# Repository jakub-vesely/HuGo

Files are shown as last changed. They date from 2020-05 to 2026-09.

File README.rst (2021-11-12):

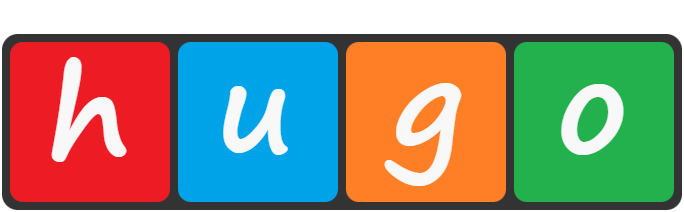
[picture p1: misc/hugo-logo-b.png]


Main goal of this project is to build a robotic car for my children. Although, it is designed as a common modular system with ambition to be used as a generic educative tool/toy.

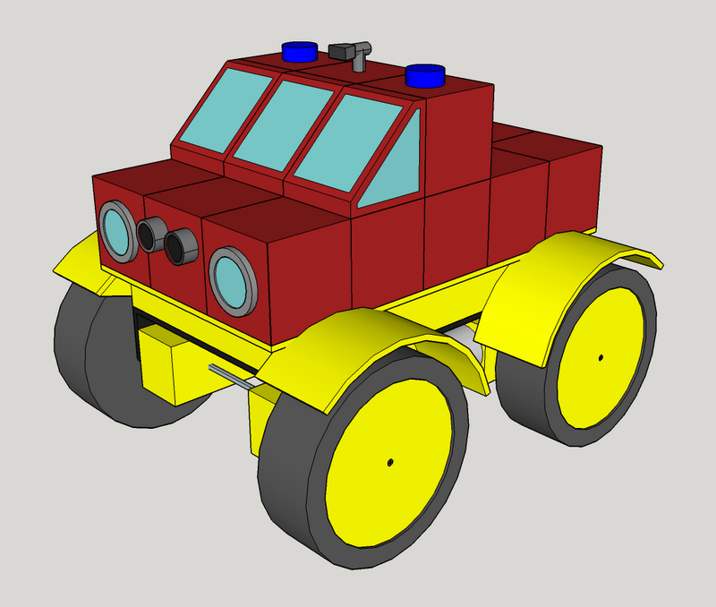
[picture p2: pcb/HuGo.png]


Current version of the Hugo project is based on ESP32, and Micropython. Extensive blocks (tyny-blocks) are based on AtTiny 412/416 micro-controllers running Arduino code.

project uses forked Micropython https://github.com/jakub-vesely/micropython. HuGo board specific code is located in the micropython/ports/esp32/boards/HUGO/ directory
and can be flashed by command:
"``idf.py -D MICROPY_BOARD=HUGO -B build-HUGO flash monitor -p <COM PORT>``"

-----
Usage
-----

Hugo specific scripts are stored in *micropython/ports/esp32/boards/HUGO/modules*. These files are already prebuilt to the firmware.
User defined behavior should be inserted to *tools/upload/events.py*. Hugo project is optimized for "events driven programming" hance all user defined actions should be added
via planned by one of these methods:

* **plan** (function, \*args, \**kwargs) for performance without expected delay
* **postpone** (delay_s, function, \*args, \**kwargs) for performance an action after a defined delay
* **repeat** (delay_s, function, \*args, \**kwargs) for continuous performed action with a defined delay

**Note**: These planner methods expects action method name defined as parameter **without brackets** followed by its parameters.

Planned action can be removed by the **kill** (handle) method. Appropriate handle is returned by method creating the event.
Programmed behavior can be uploaded to Hugo main block by launching script "``python hugo_terminal.py -f -m``" from the *tools* sub-directory.

Uploading will be performed wireless via BLE.

-----------
Development
-----------

Scripts already placed to firmware can be replaced by uploading files placed in *tools/develop* directory.
These files can be changed and uploaded to the Hugo main block by launching "``python hugo_terminal.py -f -m``" from the *tools* sub-directory.

For integration changes to firmware the original files in *micropython/ports/esp32/boards/HUGO/modules* have to be replaced by updated once.
This action can be performed by launching "``python devel_to_firmware.py``".

To build firmware esp-idf version 4 must be installed.
The build and upload to Hugo main block can be performed by launching:

"``idf.py -D MICROPY_BOARD=HUGO -B build-HUGO erase_flash flash monitor -p <COM PORT>``"
from the *micropython/ports/esp32/* directory.

The parameter *erase_flash* is recommended to remove previously uploaded scripts.

-------
Sources
-------

* Micropython homepage: https://micropython.org/
* Overview of ESP32 features is available here: https://www.espressif.com/en/products/socs/esp32/overview
* esp-idf is linked externally as recommended. Getting started guide is available here: https://docs.espressif.com/projects/esp-idf/en/stable/get-started/
* Arduino official web page https://www.arduino.cc/
* Arduino support for AtTiny series 0 and 1 https://github.com/SpenceKonde/megaTinyCore

----------
Deprecated
----------

* originally was the HuGo project based of LUA but this interpreter is not supported any more
* esp-idf project with LUA support has been moved to *src_deprecated* directory
* LUA 3.5.4 is part of the repository. Original source code is available here: https://www.lua.org/download.html

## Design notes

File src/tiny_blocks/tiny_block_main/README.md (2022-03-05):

This directory must be uploaded among Arduino libraries (Documents\Arduino\libraries) to be hugo_tiny_block_base_arduino.h visible for rest of tiny_block projects.

you can do it:
* in Windows by: mklink /D link_path source_directory_path
* in Linux by: ln -s source_directory_path link_path

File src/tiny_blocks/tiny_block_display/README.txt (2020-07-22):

hugo font derived from https://github.com/epto/epto-fonts/blob/master/font-images/img/leggibile-8x16.png
ssd1306.c derived from https://github.com/yanbe/ssd1306-esp-idf-i2c

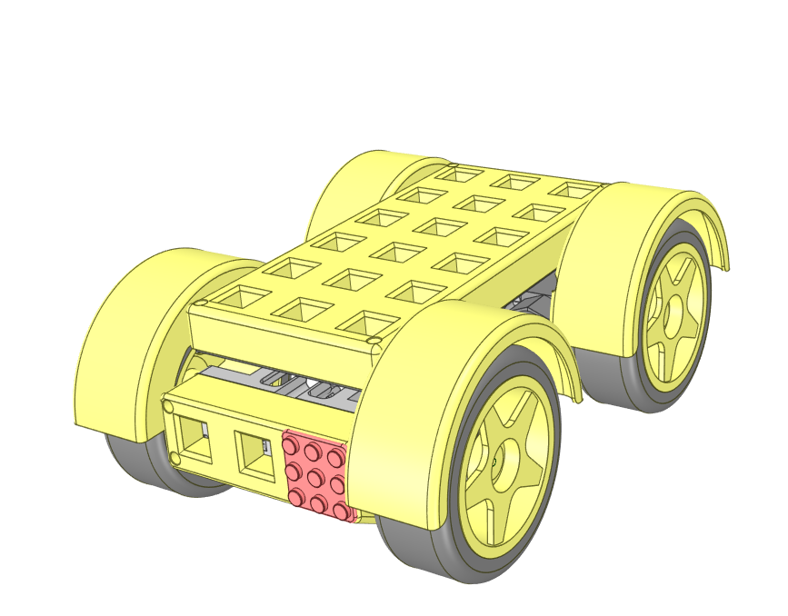
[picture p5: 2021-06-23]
shells/hugo_framework.png

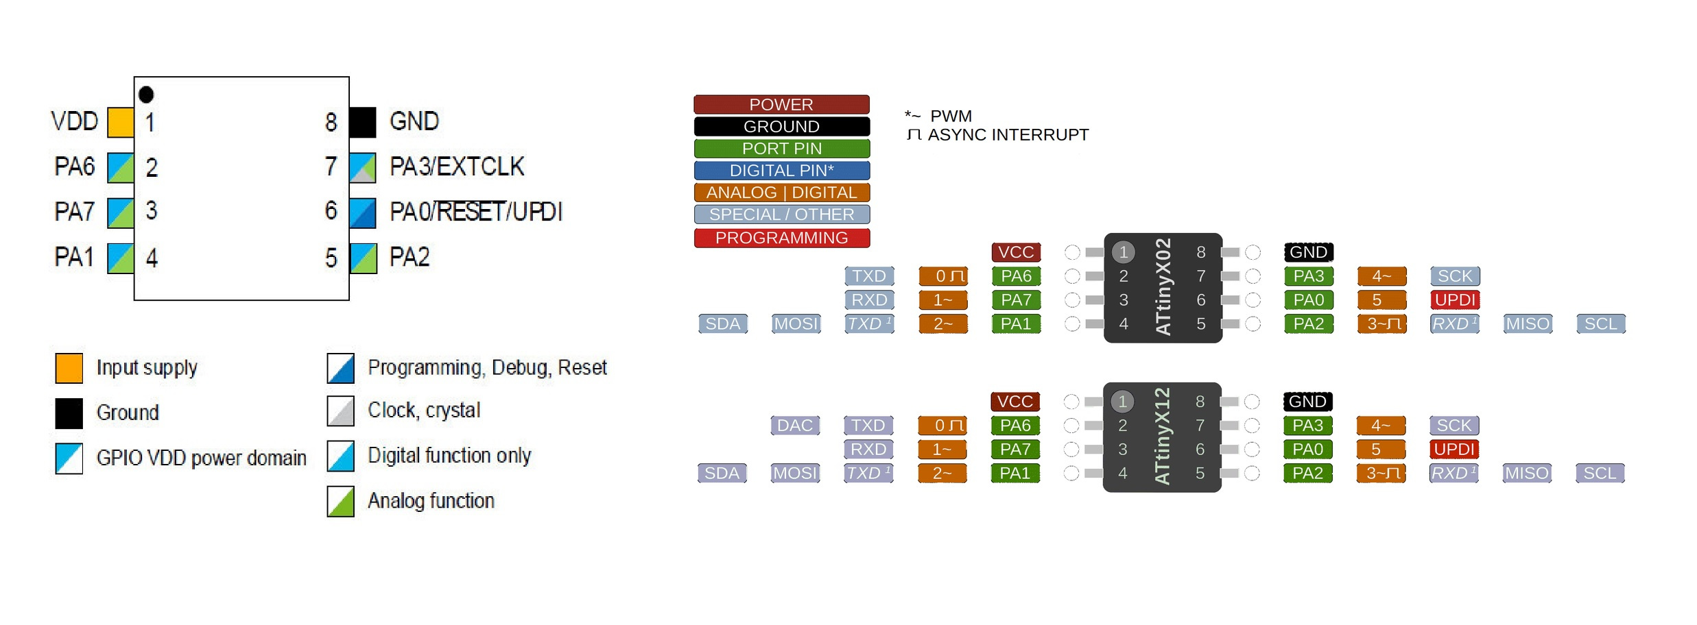
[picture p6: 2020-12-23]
pcb/datasheets/attinyX12.jpg

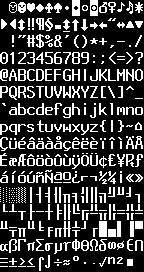
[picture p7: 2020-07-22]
src/tiny_blocks/tiny_block_display/font8x16.png

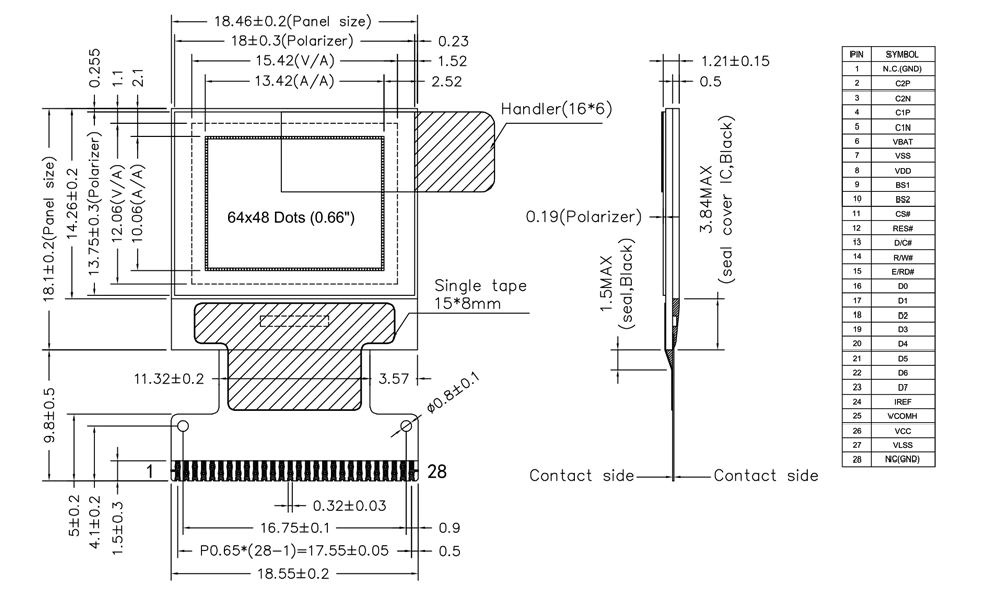
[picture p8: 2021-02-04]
pcb/datasheets/0-66-Inch-Graphic-64X48-White-LCD-28-Pin-Module-SSD1306-OLED-Micro-Display.jpg

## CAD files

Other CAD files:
pcb/hugo.skp

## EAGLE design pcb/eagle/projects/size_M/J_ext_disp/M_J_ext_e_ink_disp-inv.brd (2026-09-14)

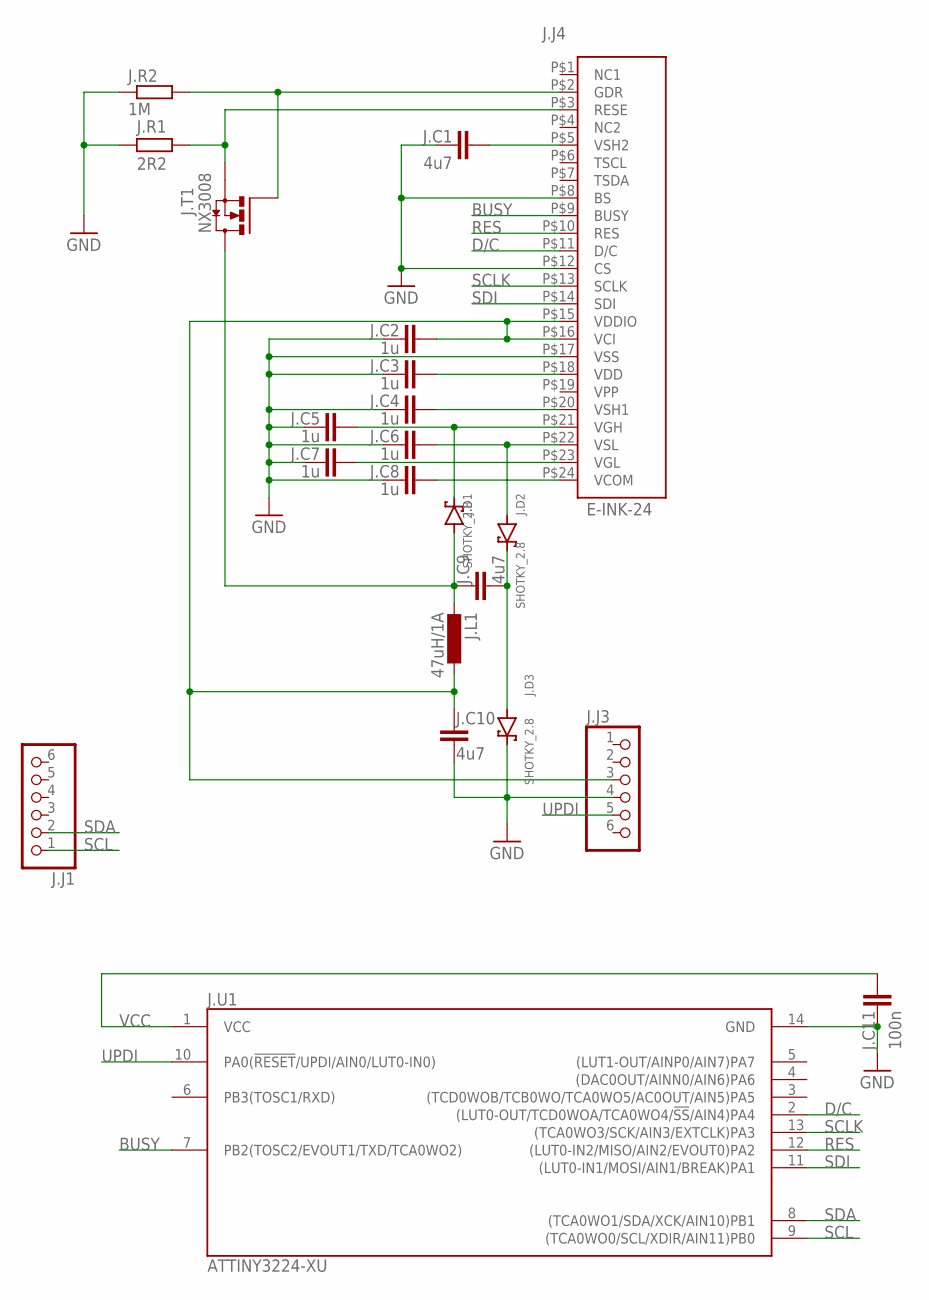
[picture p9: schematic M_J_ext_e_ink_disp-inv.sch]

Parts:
J.C1, J.C9, J.C10: 4u7; C0603
J.C2, J.C3, J.C4, J.C5, J.C6, J.C7, J.C8: 1u; C0603
J.C11: 100n; C0603
J.D1, J.D2, J.D3: SHOTKY_2.8
J.J1, J.J3: PINHD-1X6; 1X06
J.J4: E-INK-24
J.L1: 47uH/1A; L3230M
J.R1: 2R2; R0603
J.R2: 1M; R0603
J.T1: NX3008; SO23
J.U1: ATTINY3224-XU; TSSOP14

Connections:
BUSY: J.J4.P$9 (BUSY), J.U1.7 (PB2(TOSC2/EVOUT1/TXD/TCA0WO2))
D/C: J.J4.P$11 (D/C), J.U1.2 ((LUT0-OUT/TCD0WOA/TCA0WO4/!SS!/AIN4)PA4)
GND: J.C1.2, J.C2.2, J.C3.2, J.C4.2, J.C5.2, J.C6.2, J.C7.2, J.C8.2, J.C10.2, J.C11.2, J.D3.K (C), J.J3.4, J.J4.P$8 (BS), J.J4.P$12 (CS), J.J4.P$17 (VSS), J.R1.2, J.R2.1, J.U1.14 (GND)
unnamed: J.C1.1, J.J4.P$5 (VSH2)
unnamed: J.C8.1, J.J4.P$24 (VCOM)
unnamed: J.C6.1, J.D2.A, J.J4.P$22 (VSL)
unnamed: J.C5.1, J.D1.K (C), J.J4.P$21 (VGH)
unnamed: J.C9.2, J.D2.K (C), J.D3.A
unnamed: J.J4.P$3 (RESE), J.R1.1, J.T1.S
unnamed: J.C3.1, J.J4.P$18 (VDD)
unnamed: J.C4.1, J.J4.P$20 (VSH1)
unnamed: J.C9.1, J.D1.A, J.L1.2, J.T1.D
unnamed: J.C7.1, J.J4.P$23 (VGL)
unnamed: J.J4.P$2 (GDR), J.R2.2, J.T1.G
RES: J.J4.P$10 (RES), J.U1.12 ((LUT0-IN2/MISO/AIN2/EVOUT0)PA2)
SCL: J.J1.1, J.U1.9 ((TCA0WO0/SCL/XDIR/AIN11)PB0)
SCLK: J.J4.P$13 (SCLK), J.U1.13 ((TCA0WO3/SCK/AIN3/EXTCLK)PA3)
SDA: J.J1.2, J.U1.8 ((TCA0WO1/SDA/XCK/AIN10)PB1)
SDI: J.J4.P$14 (SDI), J.U1.11 ((LUT0-IN1/MOSI/AIN1/BREAK)PA1)
UPDI: J.J3.5, J.U1.10 (PA0(!RESET!/UPDI/AIN0/LUT0-IN0))
VCC: J.C2.1, J.C10.1, J.C11.1, J.J3.3, J.J4.P$15 (VDDIO), J.J4.P$16 (VCI), J.L1.1, J.U1.1 (VCC)

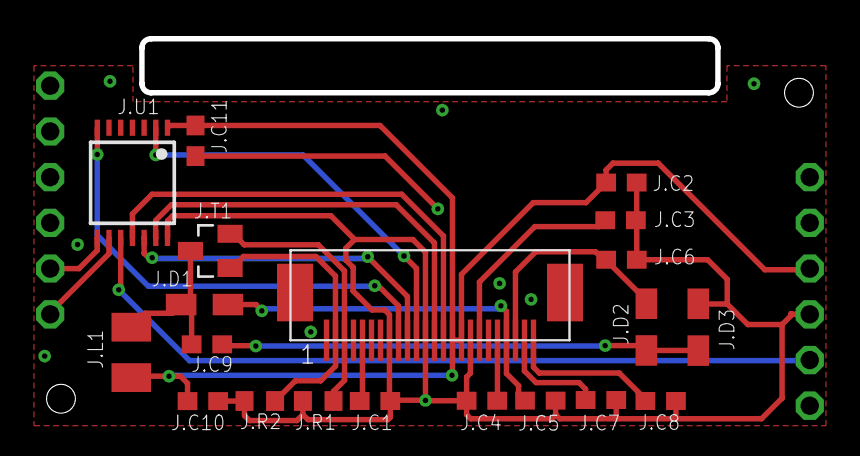
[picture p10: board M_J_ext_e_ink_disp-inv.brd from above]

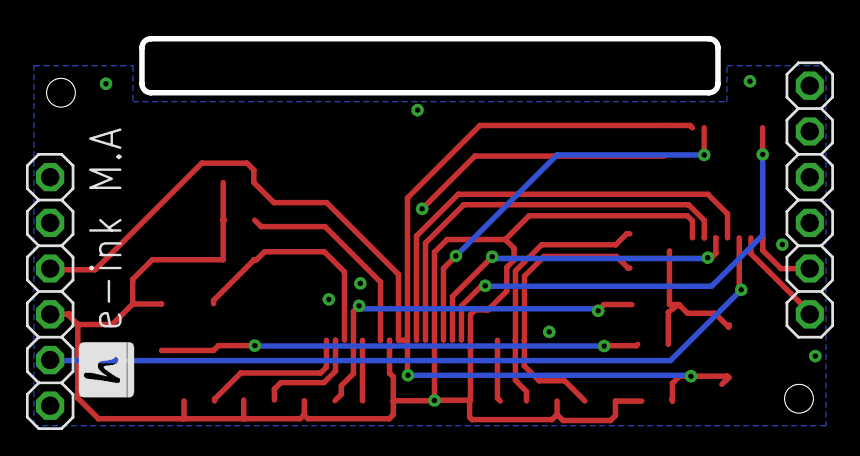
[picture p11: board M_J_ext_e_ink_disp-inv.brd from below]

Board: 2 copper layers, 32.0 x 3.0 mm, 22 parts (2 on the bottom side), 21 nets.

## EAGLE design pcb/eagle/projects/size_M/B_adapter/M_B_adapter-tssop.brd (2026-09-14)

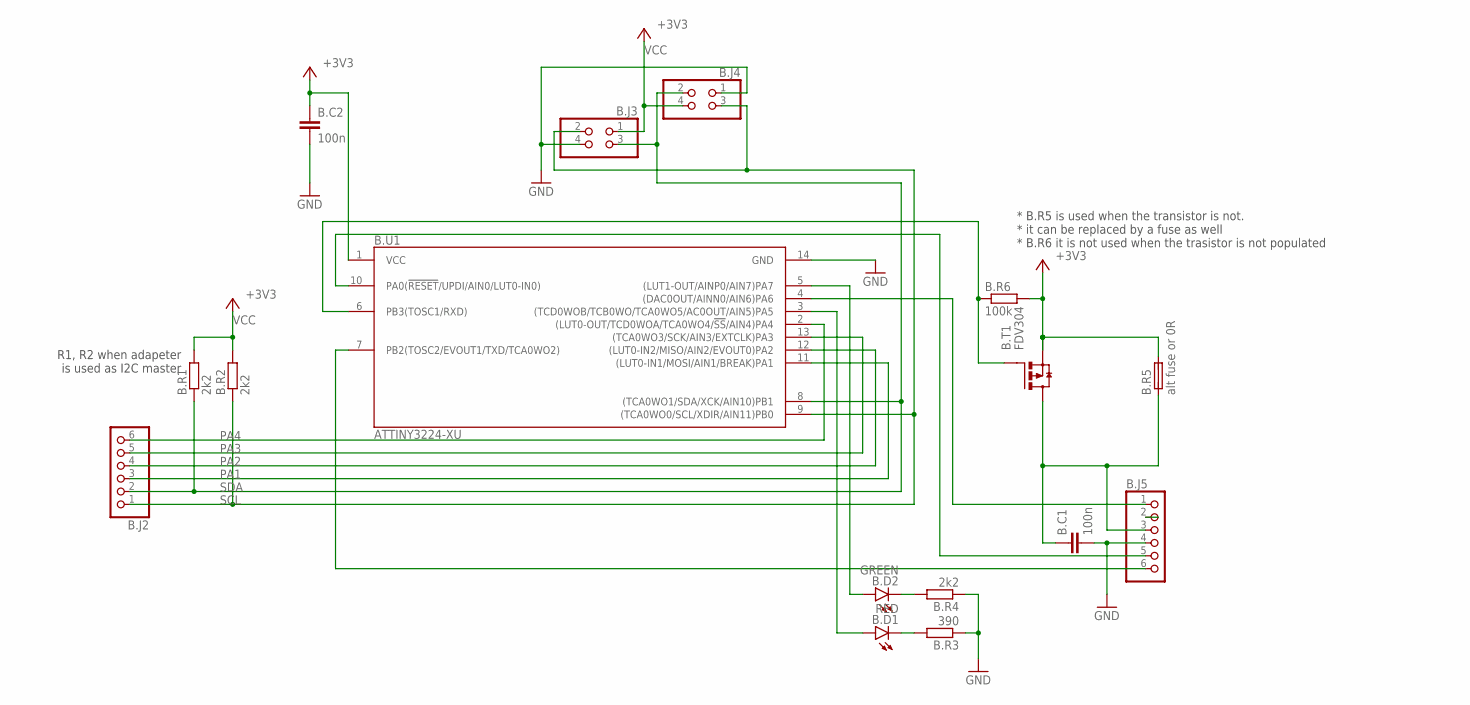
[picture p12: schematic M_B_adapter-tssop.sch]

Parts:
B.C1, B.C2: 100n; C0603
B.D1: RED; CHIP-LED0603
B.D2: GREEN; CHIP-LED0603
B.J2, B.J5: PINHD-1X6; 1X06
B.J3, B.J4: PINHD-2X2; 2X02
B.R1, B.R2, B.R4: 2k2; R0603
B.R3: 390; R0603
B.R5: alt fuse or 0R; FUSE
B.R6: 100k; R0603
B.T1: FDV304; SO23
B.U1: ATTINY3224-XU; TSSOP14

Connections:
GND: B.C1.2, B.C2.2, B.J3.4, B.J4.1, B.J5.4, B.R3.1, B.R4.1, B.U1.14 (GND)
unnamed: B.D2.C1 (C), B.R4.2
unnamed: B.D1.C1 (C), B.R3.2
unnamed: B.C1.1, B.J5.3, B.R5.1, B.T1.D
unnamed: B.D1.A1 (A), B.U1.3 ((TCD0WOB/TCB0WO/TCA0WO5/AC0OUT/AIN5)PA5)
PA1: B.J2.3, B.U1.11 ((LUT0-IN1/MOSI/AIN1/BREAK)PA1)
PA2: B.J2.4, B.U1.12 ((LUT0-IN2/MISO/AIN2/EVOUT0)PA2)
PA3: B.J2.5, B.U1.13 ((TCA0WO3/SCK/AIN3/EXTCLK)PA3)
PA4: B.J2.6, B.U1.2 ((LUT0-OUT/TCD0WOA/TCA0WO4/!SS!/AIN4)PA4)
PA6: B.J5.1, B.U1.4 ((DAC0OUT/AINN0/AIN6)PA6)
PA7: B.D2.A1 (A), B.U1.5 ((LUT1-OUT/AINP0/AIN7)PA7)
PB2: B.J5.6, B.U1.7 (PB2(TOSC2/EVOUT1/TXD/TCA0WO2))
PB3: B.R6.1, B.T1.G, B.U1.6 (PB3(TOSC1/RXD))
SCL: B.J2.1, B.J3.2, B.J4.3, B.R2.1, B.U1.9 ((TCA0WO0/SCL/XDIR/AIN11)PB0)
SDA: B.J2.2, B.J3.3, B.J4.2, B.R1.1, B.U1.8 ((TCA0WO1/SDA/XCK/AIN10)PB1)
UPDI: B.J5.5, B.U1.10 (PA0(!RESET!/UPDI/AIN0/LUT0-IN0))
VBAT: B.J5.2
VCC: B.C2.1, B.J3.1, B.J4.4, B.R1.2, B.R2.2, B.R5.2, B.R6.2, B.T1.S, B.U1.1 (VCC)

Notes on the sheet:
* B.R5 is used when the transistor is not. * it can be replaced by a fuse as well * B.R6 it is not used when the trasistor is not populated
R1, R2 when adapeter is used as I2C master

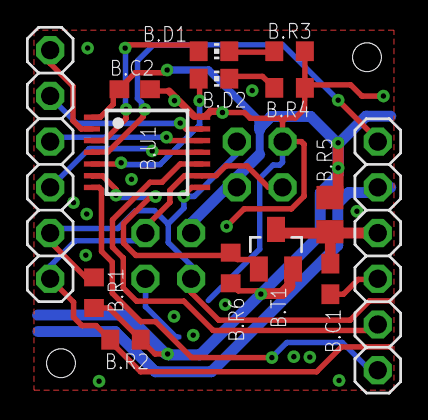
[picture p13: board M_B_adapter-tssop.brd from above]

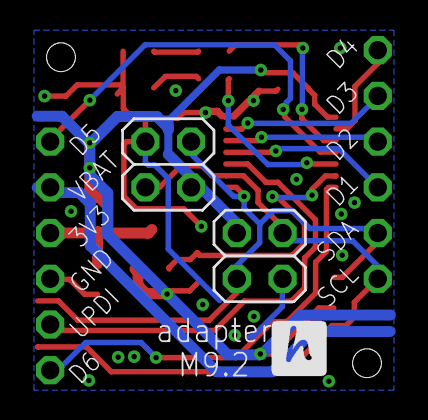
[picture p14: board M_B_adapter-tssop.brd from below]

Board: 2 copper layers, 16 parts (2 on the bottom side), 17 nets.

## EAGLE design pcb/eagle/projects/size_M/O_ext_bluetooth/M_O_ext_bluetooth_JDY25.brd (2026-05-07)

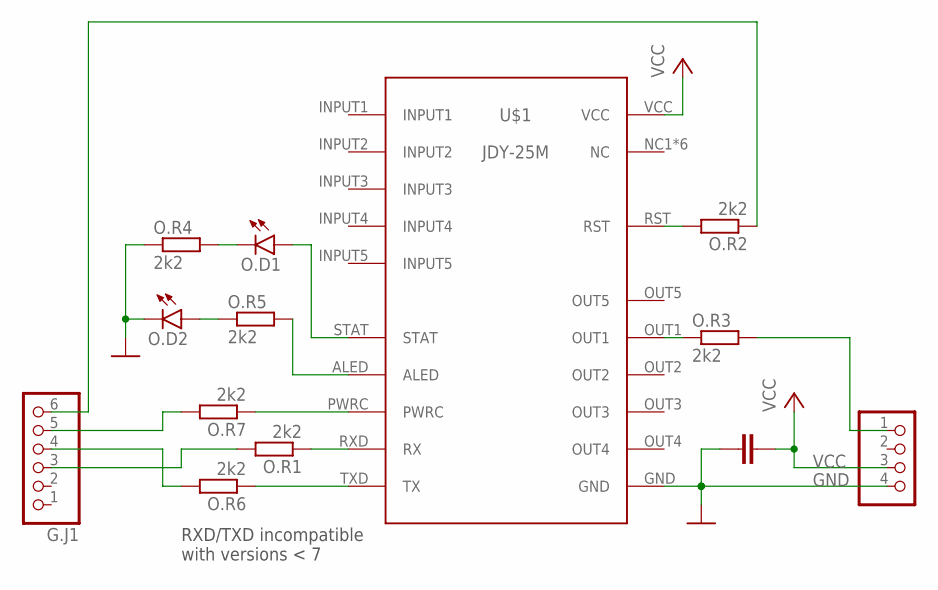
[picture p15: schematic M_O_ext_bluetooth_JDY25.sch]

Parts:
G.J1: PINHD-1X6; 1X06
G.J2: PINHD-1X4; 1X04
O.C1: 100n; C0603
O.D1, O.D2: LEDCHIP-LED0603; CHIP-LED0603
O.R1, O.R2, O.R3, O.R4, O.R5, O.R6, O.R7: 2k2; R0603
U$1: JDY-25

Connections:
GND: G.J2.4, O.C1.1, O.D2.C1 (C), O.R4.1, U$1.GND
unnamed: O.R1.1, U$1.RXD (RX)
unnamed: O.R6.1, U$1.TXD (TX)
unnamed: G.J1.5, O.R7.2
unnamed: O.R7.1, U$1.PWRC
unnamed: G.J2.1, O.R3.2
unnamed: O.R5.2, U$1.ALED
unnamed: O.D1.A1 (A), U$1.STAT
unnamed: G.J1.6, O.R2.1
unnamed: O.D1.C1 (C), O.R4.2
unnamed: O.D2.A1 (A), O.R5.1
unnamed: O.R3.1, U$1.OUT1
unnamed: O.R2.2, U$1.RST
RX: G.J1.4, O.R6.2
TX: G.J1.3, O.R1.2
VCC: G.J2.3, O.C1.2, U$1.VCC

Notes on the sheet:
RXD/TXD incompatible with versions < 7

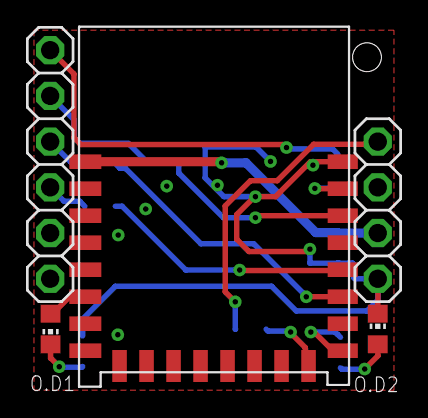
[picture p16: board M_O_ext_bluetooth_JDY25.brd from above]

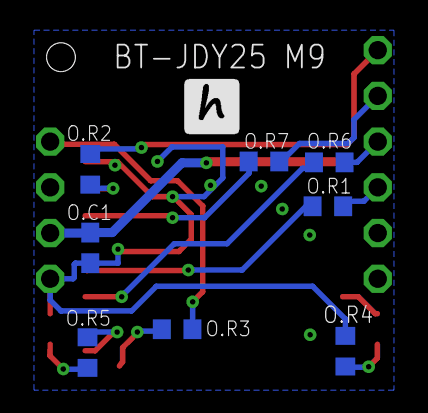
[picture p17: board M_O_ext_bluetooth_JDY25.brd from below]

Board: 2 copper layers, 13 parts (8 on the bottom side), 16 nets.

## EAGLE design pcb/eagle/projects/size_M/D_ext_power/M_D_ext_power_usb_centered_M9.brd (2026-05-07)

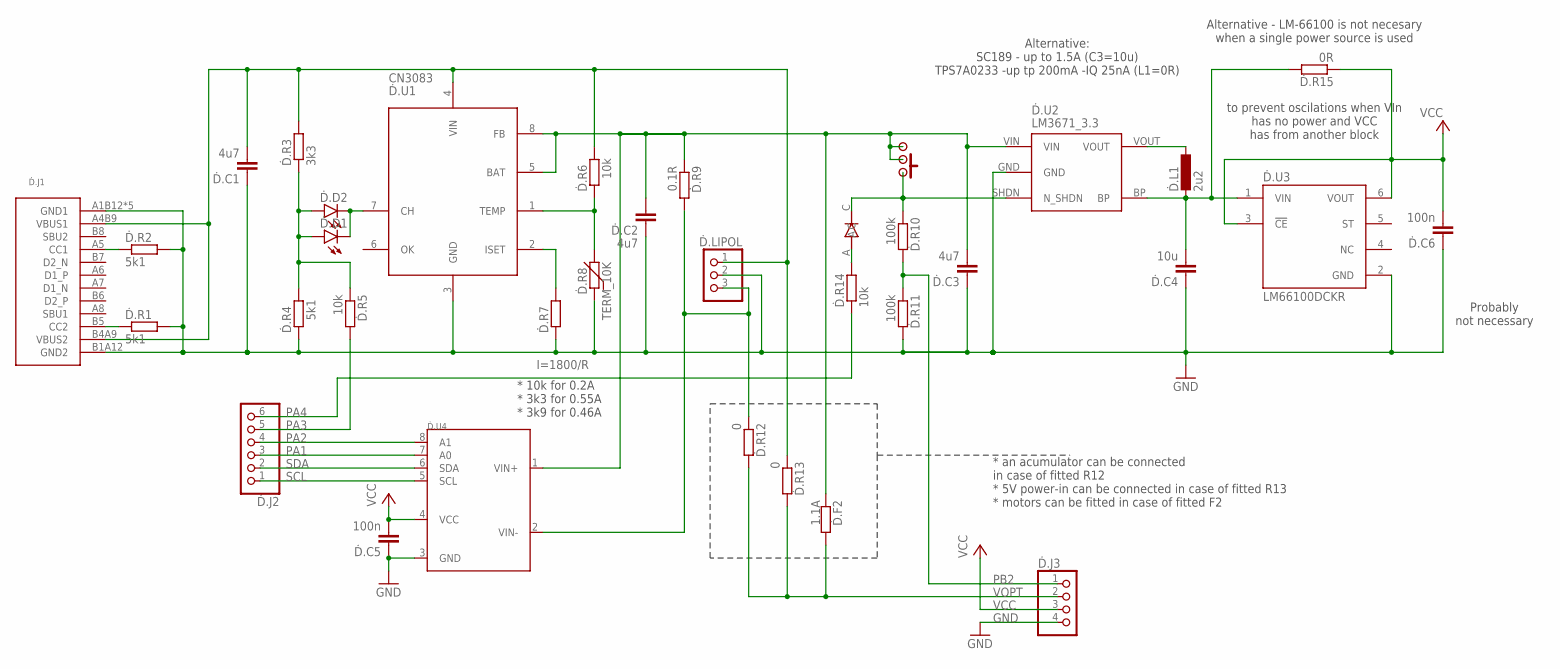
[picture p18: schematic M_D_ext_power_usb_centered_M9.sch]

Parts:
Ḋ.BTN: SWITCH
Ḋ.C1, Ḋ.C2, Ḋ.C3: 4u7; C0603
Ḋ.C4: 10u; C0603
Ḋ.C5, Ḋ.C6: 100n; C0603
Ḋ.D1, Ḋ.D2: LEDCHIP-LED0603; CHIP-LED0603
Ḋ.D3: DIODE
Ḋ.F2: 1.1A; R0805
Ḋ.J1: USB-C
Ḋ.J2: PINHD-1X6; 1X06
Ḋ.J3: PINHD-1X4; 1X04
Ḋ.L1: 2u2; L3230M
Ḋ.LIPOL: PINHEAD-1X3-2; 1X-03-2
Ḋ.R1, Ḋ.R2, Ḋ.R4: 5k1; R0603
Ḋ.R3: 3k3; R0603
Ḋ.R5, Ḋ.R6, Ḋ.R14: 10k; R0603
Ḋ.R7: I=1800/R; R0603
Ḋ.R8: TERM_10K; THERM
Ḋ.R9: 0.1R; R0805
Ḋ.R10, Ḋ.R11: 100k; R0603
Ḋ.R12, Ḋ.R13: 0; R0603
Ḋ.R15: 0R; R0603
Ḋ.U1: CN3083; SOP8
Ḋ.U2: LM3671_3.3; SOT32-5
Ḋ.U3: LM66100DCKR; SOT65P210X110-6N
Ḋ.U4: INA219; SOT23-8

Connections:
5V: Ḋ.C1.2, Ḋ.J1.A4B9 (VBUS1), Ḋ.J1.B4A9 (VBUS2), Ḋ.LIPOL.1, Ḋ.R3.2, Ḋ.R6.2, Ḋ.R13.1, Ḋ.U1.4 (VIN)
CHRG: Ḋ.D1.A1 (A), Ḋ.D2.A1 (A), Ḋ.R3.1, Ḋ.R4.2, Ḋ.R5.1
GND: Ḋ.C1.1, Ḋ.C2.1, Ḋ.C3.1, Ḋ.C4.1, Ḋ.C5.1, Ḋ.C6.1, Ḋ.J1.A1B12 (GND1), Ḋ.J1.B1A12 (GND2), Ḋ.J1.SH1 (GND1), Ḋ.J1.SH2 (GND1), Ḋ.J1.SH3 (GND1), Ḋ.J1.SH4 (GND1), Ḋ.J3.4, Ḋ.LIPOL.2, Ḋ.R1.2, Ḋ.R2.2, Ḋ.R4.1, Ḋ.R7.1, Ḋ.R8.1, Ḋ.R11.2, Ḋ.U1.3 (GND), Ḋ.U2.GND, Ḋ.U3.2 (GND), Ḋ.U4.3 (GND)
IN+: Ḋ.BTN.P$2, Ḋ.BTN.P$3, Ḋ.BTN.P$4, Ḋ.BTN.P$6, Ḋ.C2.2, Ḋ.C3.2, Ḋ.F2.1, Ḋ.R9.1, Ḋ.U1.5 (BAT), Ḋ.U1.8 (FB), Ḋ.U2.VIN, Ḋ.U4.1 (VIN+)
IN-: Ḋ.LIPOL.3, Ḋ.R9.2, Ḋ.R12.1, Ḋ.U4.2 (VIN-)
unnamed: Ḋ.L1.1, Ḋ.U2.VOUT
unnamed: Ḋ.D1.C1 (C), Ḋ.D2.C1 (C), Ḋ.U1.7 (CH)
unnamed: Ḋ.J1.B5 (CC2), Ḋ.R1.1
unnamed: Ḋ.D3.A, Ḋ.R14.2
unnamed: Ḋ.J1.A5 (CC1), Ḋ.R2.1
unnamed: Ḋ.R7.2, Ḋ.U1.2 (ISET)
unnamed: Ḋ.R6.1, Ḋ.R8.2, Ḋ.U1.1 (TEMP)
unnamed: Ḋ.BTN.P$1, Ḋ.BTN.P$5, Ḋ.BTN.P$7, Ḋ.D3.C, Ḋ.R10.1, Ḋ.U2.SHDN (N_SHDN)
PA1: Ḋ.J2.3, Ḋ.U4.7 (A0)
PA2: Ḋ.J2.4, Ḋ.U4.8 (A1)
PA3: Ḋ.J2.5, Ḋ.R5.2
PA4: Ḋ.J2.6, Ḋ.R14.1
PB2: Ḋ.J3.1, Ḋ.R10.2, Ḋ.R11.1
SCL: Ḋ.J2.1, Ḋ.U4.5 (SCL)
SDA: Ḋ.J2.2, Ḋ.U4.6 (SDA)
VCC: Ḋ.C5.2, Ḋ.C6.2, Ḋ.J3.3, Ḋ.R15.1, Ḋ.U3.3 (!CE), Ḋ.U3.6 (VOUT), Ḋ.U4.4 (VCC)
VCC1: Ḋ.C4.2, Ḋ.L1.2, Ḋ.R15.2, Ḋ.U2.BP, Ḋ.U3.1 (VIN)
VOPT: Ḋ.F2.2, Ḋ.J3.2, Ḋ.R12.2, Ḋ.R13.2

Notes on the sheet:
* an acumulator can be connected in case of fitted R12 * 5V power-in can be connected in case of fitted R13 * motors can be fitted in case of fitted F2
to prevent oscilations when VIn has no power and VCC has from another block
* 10k for 0.2A * 3k3 for 0.55A * 3k9 for 0.46A
Alternative: SC189 - up to 1.5A (C3=10u) TPS7A0233 -up tp 200mA -IQ 25nA (L1=0R)
Probably not necessary
Alternative - LM-66100 is not necesary when a single power source is used

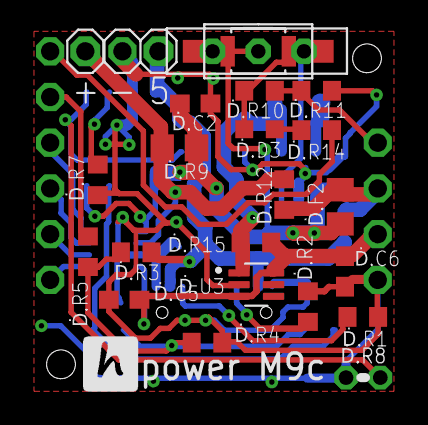
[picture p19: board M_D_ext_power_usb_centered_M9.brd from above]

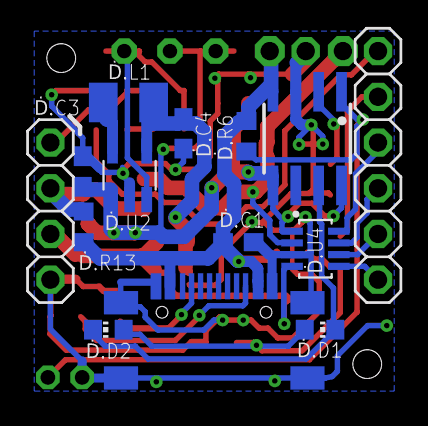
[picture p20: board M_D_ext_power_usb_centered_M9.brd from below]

Board: 2 copper layers, 35 parts (14 on the bottom side), 23 nets.

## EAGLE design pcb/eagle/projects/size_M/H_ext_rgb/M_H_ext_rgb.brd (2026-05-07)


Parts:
H.D1: RGB_WW-FCE50TC-Q1
H.J1, H.J2: PINHD-1X6; 1X06
H.R1, H.R2, H.R3: 82; R0603

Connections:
GND: H.D1.4, H.D1.5, H.D1.6, H.J1.4
unnamed: H.D1.1, H.R1.2
unnamed: H.D1.3, H.R3.2
unnamed: H.D1.2, H.R2.2
unnamed: H.J1.6, H.R1.1
unnamed: H.J2.6, H.R2.1
unnamed: H.J2.5, H.R3.1
VDD: H.J1.3


Board: 2 copper layers, 6 parts (0 on the bottom side), 7 nets.

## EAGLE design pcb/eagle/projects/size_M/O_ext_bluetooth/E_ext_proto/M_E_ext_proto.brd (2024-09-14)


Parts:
JP1, JP2: PINHD-1X6; 1X06
JP3, JP11: PINHD-1X5; 1X05
U$1, U$2, U$3, U$4, U$5, U$6, U$7, U$8: PINHD-1X5_AUTO; 1X5_AUTO

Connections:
GND: JP3.4, JP11.4
unnamed: JP1.5, JP2.5
unnamed: JP1.4, JP2.4
unnamed: JP1.3, JP2.3
unnamed: JP1.2, JP2.2
unnamed: JP1.1, JP2.1
unnamed: JP3.5, JP11.5
unnamed: JP3.2, JP11.2
unnamed: JP3.1, JP11.1
unnamed: JP1.6, JP2.6
unnamed: JP3.3, JP11.3


Board: 2 copper layers, 12 parts (0 on the bottom side), 11 nets.

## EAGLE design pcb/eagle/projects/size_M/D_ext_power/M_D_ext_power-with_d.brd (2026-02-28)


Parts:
D.C1, D.C2, D.C3: 4u7; C0603
D.C4: 10u; C0603
D.C5, D.C6, D.C7: 100n; C0603
D.D1: LED_1.8
D.D3: SHOTKY_2.8 or another diode; SHOTKY_2.8
D.F2: 1.1A; R0805
D.J2: PINHD-1X6; 1X06
D.J3: PINHD-1X4; 1X04
D.L1: 2u2; L3230M
D.LIPOL: PINHEAD-1X3-2; 1X-03-2
D.ON/OFF/RESET: SWITCH
D.R1, D.R2, D.R4: 5k1; R0603
D.R3: 3k3; R0603
D.R5, D.R13, D.R14: 0R; R0603
D.R6, D.R8: 10k; R0603
D.R7: I=1800/R; R0603
D.R9: TERM_10K; THERM
D.R10: 0.1; R0805
D.R11: 390k; R0603
D.R12: 100k; R0603
D.U1: CN3083; SOP8
D.U2: SN74AUP1G80; DCK0005A_M
D.U3: LM3671_3.3; SOT32-5
D.U4: LM66100DCKR; SOT65P210X110-6N
D.U5: INA219; SOT23-8
U$1: USB-C

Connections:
5V: D.C1.2, D.LIPOL.1, D.R3.2, D.R8.2, D.R13.1, D.U1.4 (VIN), U$1.A4B9 (VBUS1), U$1.B4A9 (VBUS2)
CHRG: D.D1.2 (A), D.R3.1, D.R4.2, D.R6.1
GND: D.C1.1, D.C2.1, D.C3.1, D.C4.1, D.C5.1, D.C6.1, D.C7.1, D.J3.4, D.LIPOL.2, D.R1.2, D.R2.2, D.R4.1, D.R7.1, D.R9.1, D.R11.2, D.U1.3 (GND), D.U2.3 (GND), D.U3.GND, D.U4.2 (GND), D.U5.3 (GND), U$1.A1B12 (GND1), U$1.B1A12 (GND2), U$1.SH1 (GND1), U$1.SH2 (GND1), U$1.SH3 (GND1), U$1.SH4 (GND1)
IN+: D.C2.2, D.C3.2, D.C7.2, D.F2.1, D.ON/OFF/RESET.P$2, D.ON/OFF/RESET.P$3, D.ON/OFF/RESET.P$4, D.ON/OFF/RESET.P$6, D.R10.1, D.U1.5 (BAT), D.U1.8 (FB), D.U2.5 (VCC), D.U3.VIN, D.U5.1 (VIN+)
IN-: D.LIPOL.3, D.R5.1, D.R10.2, D.U5.2 (VIN-)
unnamed: D.L1.1, D.U3.VOUT
unnamed: D.D1.1 (K), D.U1.7 (CH)
unnamed: D.R1.1, U$1.B5 (CC2)
unnamed: D.D3.A, D.R12.2
unnamed: D.R2.1, U$1.A5 (CC1)
unnamed: D.R7.2, D.U1.2 (ISET)
unnamed: D.R8.1, D.R9.2, D.U1.1 (TEMP)
unnamed: D.R14.2, D.U2.1 (D), D.U2.4 (Q_N), D.U3.SHDN (N_SHDN)
unnamed: D.D3.K (C), D.ON/OFF/RESET.P$1, D.ON/OFF/RESET.P$5, D.ON/OFF/RESET.P$7, D.R11.1, D.R14.1, D.U2.2 (CLK)
PA1: D.J2.3, D.U5.7 (A0)
PA2: D.J2.4, D.U5.8 (A1)
PA3: D.J2.5, D.R6.2
PA5-1: D.J3.1, D.R12.1
SCL: D.J2.1, D.U5.5 (SCL)
SDA: D.J2.2, D.U5.6 (SDA)
VCC: D.C5.2, D.C6.2, D.J3.3, D.U4.3 (!CE), D.U4.6 (VOUT), D.U5.4 (VCC)
VCC1: D.C4.2, D.L1.2, D.U3.BP, D.U4.1 (VIN)
VOPT: D.F2.2, D.J3.2, D.R5.2, D.R13.2

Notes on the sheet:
* an acumulator can be connected in case of fitted R5 * 5V power-in can be connected in case of fitted R13 * motors can be fitted in case of fitted F2
EXPERIMENTAL to prevent oscilations when VIn has no power and VCC has from another block
* 10k for 0.2A * 3k3 for 0.55A * 3k9 for 0.46A
Alternative SC189 (C3=10u;L1=2u2,C4=10u;L1=1u, C4=22u) or TPS7A0233 for low power consumtion in idle. In this case use 0R instead of L1
Probably not necessary
Alternative for switch instead of U2 and D3 and R12



Board: 2 copper layers, 35 parts (14 on the bottom side), 23 nets.

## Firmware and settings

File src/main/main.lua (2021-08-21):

--[[
    Copyright (c) 2020 jakub-vesely
    This software is published under MIT license. Full text of the licence is available at https://opensource.org/licenses/MIT
--]]

--local gpio = require "gpio"
--local chassis = require("chassis")

-- local program_started = luvent.newEvent()
-- local led_state = 1

-- local function connect()
--     program_started:addAction(
--         function ()
--             print("action")
--             built_in_led.change_state(1)
--         end
--     )
-- end

-- connect()
-- program_started:trigger()

-- function After_time()
--     if led_state == 0 then
--         led_state = 1
--     else
--         led_state = 0
--     end
--     built_in_led.change_state(led_state)
--     timer.call_after_time(After_time, 0.5)
-- end

-- timer.call_after_time(After_time, 3)

-- local pwm_duty = 0
-- Pwm_change = function()
--     pwm_duty = pwm_duty + 1
--     if pwm_duty > 10 then
--         pwm_duty = 0
--     end
--     gpio.set_pwm_duty(pwm_duty * 10)
--     timer.call_after_time(Pwm_change, 0.3)
-- end
-- gpio.init_pin_for_pwm(12, 100, pwm_duty)
-- timer.call_after_time(Pwm_change, 0.3)

-- local rotate = 0
-- function ChangeDirection()
--     if rotate == 1 then
--         rotate = 0
--         gpio.set_logic_value(32, 0)
--         gpio.set_logic_value(33, 1)
--     else
--         rotate = 1
--         gpio.set_logic_value(32, 1)
--         gpio.set_logic_value(33, 0)
--     end
--     timer.call_after_time(ChangeDirection, 1)
-- end

-- function Right()
--     chassis.rotate_counterclockwise()
--     timer.call_after_time(Stop, 1)
-- end

-- function Backward()
--     chassis.go_backward()
--     timer.call_after_time(Right, 1)
-- end

-- function Left()
--     chassis.rotate_clockwise()
--     timer.call_after_time(Backward, 1)
-- end

-- function Forward()
--     chassis.go_forward()
--     timer.call_after_time(Left, 1)
-- end

-- function Stop()
--     chassis.stop()
--     timer.call_after_time(Forward, 1)
-- end
-- timer.call_after_time(Stop, 1)

-- gpio.init_pin_for_out(25)
-- gpio.init_pin_for_out(26)
-- gpio.set_logic_value(25, 0)
-- gpio.set_logic_value(26, 0)

-- gpio.init_pin_for_out(32)
-- gpio.init_pin_for_out(33)
-- gpio.set_logic_value(32, 1)
-- gpio.set_logic_value(33, 0)
-- timer.call_after_time(ChangeDirection, 1)

local hours = 0
local minutes = 0
local seconds = 0

local function value_getter(property_id)
    print("called getter for peroperty_id", property_id)
    return 42
end

local function value_setter(property_id, value)
    print("called setter for peroperty_id", property_id, value)
    if property_id == 1 then
        hours = value
    elseif property_id == 2 then
        minutes = value
    elseif property_id == 3 then
        seconds = value
    else
        return false
    end
    return true
end

local function commander(command_id, data)
    print("called commander", command_id, data)
    return true
end

local ble = require "ble"
ble.register_getter(1, value_getter)
ble.register_setter(1, value_setter)
ble.register_setter(2, value_setter)
ble.register_setter(3, value_setter)
ble.register_command(1, commander)
print("behavior definition started")
local block_factory = require "block_factory"
local timer = require("timer")

local display = block_factory.display_block(0x02)
display:print_text_8x8(0, 0, 64, 48, "A1A2A3a4\nB1B2B3b\nC1C2C3c\nD1D2D3d\nE1E2E3e\nF1F2F3f4", true)
display:showtime()
local counter = 1
function display_counter()
    display:clean()
    --local text =  ":" tostring(math.floor(minutes)) ":" tostring(math.floor(seconds))
    --print(text)
    -- if hours > 9 then
    --     display:print_text_8x8(0, 0, 64, 48, tostring(math.floor(hours)), true)
    -- else
    --     display:print_text_8x8(8, 0, 64, 48, tostring(math.floor(hours)), true)
    -- end
    -- display:print_text_8x8(16, 0, 64, 48, ":", true)

    -- if minutes > 9 then
    --     display:print_text_8x8(24, 0, 64, 48, tostring(math.floor(minutes)), true)
    -- else
    --     display:print_text_8x8(24, 0, 64, 48, "0", true)
    --     display:print_text_8x8(32, 0, 64, 48, tostring(math.floor(minutes)), true)
    -- end

    --display:print_text_8x16(10, 20, 64, 48, tostring(math.floor(seconds)), true)

    display:print_text_8x8(10, 20, 64, 48, tostring(counter), true)
    counter = counter    + 1
    display:showtime()
    --counter = counter + 1
    timer.call_after_time(display_counter, 1)
end
display_counter()

--display:set_new_i2c_address(0x06)

-- display.clean()
-- print("disp cleaned")
-- display.print_text_8x16(0, 0, 64, 32, "hallo", true)
-- print("disp text")
-- display.showtime()
-- print("disp shown")
-- local mpu = require("mpu9250")
-- local chassis = require("chassis")

-- mpu.add_measured_action(
--     function()
--         local value_accel_y = string.format("accelY: %4.2f", mpu.get_accel_y())
--         local value_gyro_z = string.format("gyroZ: %4.2f", mpu.get_gyro_z())
--         display.clean()
--         display.print_text_8x16(0, 0, 64, 32, value_accel_x, true)
--         display.print_text_8x16(0, 0, 128, 32, value_accel_y, true)
--         display.print_text_8x16(0, 16, 128, 32, value_gyro_z, true)
--         display.showtime()
--         -- print("value_accel_y %s", value_accel_y)
--         if mpu.get_accel_y()< -1 then
--             chassis.stop()
--         end
--     end
-- )

-- local ir_remote = require "ir_remote"
-- ir_remote.add_data_recoveved_action(
--     function (addr, code, repeated)
--         if repeated == 1 then
--             return
--         end
--         print("action", code)
--         if code == 59160 or code == 60690 then
--             print("forward")
--             chassis.go_forward()
--         elseif code == 44370 or code == 60435 then
--             print("back")
--             chassis.go_backward()
--         elseif code == 42330 or code == 61200 then
--             chassis.rotate_clockwise()
--         elseif code == 63240 or code == 60945 then
--             chassis.rotate_counterclockwise()
--         elseif code == 58140 or code == 46920 then
--             chassis.stop()
--         else
--             print("unknown command")
--         end
--     end
-- )


-- local rgb = block_factory.rgb_led_block(0x04)
-- rgb:set_new_i2c_address(0x04)
-- --local counter = 0;
-- --local reverse = false;

-- function set_on()
--     rgb:set_on()
--     timer.call_after_time(set_off, 1)
-- end

-- function set_off()
--     rgb:set_off()
--     timer.call_after_time(set_red, 1)
-- end

-- set_on()

-- function set_red()
--      rgb:set_color(rgb.color.red)
--      timer.call_after_time(set_green, 1)
-- end
-- function set_green()
--     rgb:set_color(rgb.color.green)
--     timer.call_after_time(set_red, 1)
-- end
-- set_red()

-- function set_blue()
--     rgb:set_color(rgb.color.blue)
--     timer.call_after_time(set_on, 1)
-- end
-- set_red()

    -- function led_change()
--     rgb:set_values(255 - counter, counter, 0)

--     if reverse then
--         if counter == 0 then
--             reverse = false
--             counter = 1
--         else
--             counter = counter - 1
--         end
--     else
--         if counter == 255 then
--             reverse = true
--             counter = 255
--         else
--             counter = counter + 1
--         end
--     end

--     timer.call_after_time(led_change, 0.1)
-- end


-- timer.call_after_time(led_change, 1)



--
-- local motor_driver_block = block_factory.motor_driver_block(0x02)
-- --motor_driver_block:set_new_i2c_address(0x05)

-- function start_motor()
--     local count1 = motor_driver_block:get_counter(1)
--     local count2 = motor_driver_block:get_counter(2)
--     print("count1", count1, "count2", count2)

--     print(count1)
--     if count1 < 1000 then
--         motor_driver_block:speed_100(1)
--         motor_driver_block:speed_100(2)
--         timer.call_after_time(stop_motor, 1)
--         timer.call_after_time(stop_motor, 2)
--     end

-- end

-- function stop_motor()
--     motor_driver_block:speed_0(1)
--     timer.call_after_time(start_motor, 1)
-- end

-- --timer.call_after_time(start_motor, 1)
-- motor_driver_block:power_on(1)
-- motor_driver_block:power_on(2)
-- motor_driver_block:turn_clockwise(1)
-- motor_driver_block:turn_anticlockwise(2)
-- -- motor_driver_block:speed_100(1)
-- -- motor_driver_block:speed_100(2)
-- start_motor()


-- local power_block = block_factory.power_block(0x03)
-- --power_block:set_new_i2c_address(0x03)
-- local function charging()
--     if (power_block:is_charging()) then
--         rgb:set_color(rgb.color.red)
--     else
--         rgb:set_color(rgb.color.green)
--     end
--     timer.call_after_time(charging, 0.5)
-- end
-- charging()

--

-- local function charging()
--     print("charging", power_block:is_charging())
--     print("voltage", power_block:get_voltage())
--     print("current", power_block:get_current_ma())
--     timer.call_after_time(charging, 1)
-- end

--charging()

--print("i2c_address", power_block:get_i2c_address())
--print("power ina address", power_block:get_ina_i2c_address())

--power_block:set_ina_i2c_address(power_block.InaAddresses.INA_I2C_0x45)

--print("power ina address", power_block:get_ina_i2c_address())

--power_block:set_new_i2c_address(0x04)
--print("power address0", power_block:get_ina_i2c_address())
-- power_block:set_ina_a0a1(1)
-- print("power address1", power_block:get_ina_i2c_address())
-- power_block:set_ina_a0a1(2)
-- print("power address2", power_block:get_ina_i2c_address())
-- power_block:set_ina_a0a1(3)
-- print("power address3", power_block:get_ina_i2c_address())


-- local ir = block_factory.ir_receiver_block(0x02)
-- -- ir:set_new_i2c_address(0x06)

-- function get_ir()
--     local ir_data = ir:get_ir_data();
--     if (ir_data ~= 0) then
--         print("ir_data", ir_data)
--     end
--     timer.call_after_time(get_ir, 1)
-- end
-- get_ir()
print("behavior definition finished")

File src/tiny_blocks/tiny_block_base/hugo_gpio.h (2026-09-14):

#pragma once

#ifndef HUGO_PCB_VERSION
#   error HUGO_PCB_VERSION is not defined
#else
#   if HUGO_PCB_VERSION < 7
#       define HUGO_PIN_D1 PIN_PA7
#       define HUGO_PIN_D2 PIN_PA6
#       define HUGO_PIN_D3 PIN_PA3

#       if defined(__AVR_ATtiny412__)
//Serial communication for old PCBs is not implemented any more
//#           define HUGO_PIN_RXD PIN_PB2
//#           define HUGO_PIN_TXD PIN_PB3

#       else
//#           define HUGO_PIN_RXD
//#           define HUGO_PIN_TXD
#       endif

#       define HUGO_PIN_SDA PIN_PA1
#       define HUGO_PIN_SCL PIN_PA2
//#       define HUGO_PIN_MOSI
//#       define HUGO_PIN_MISO
//#       define HUGO_PIN_SCK
//#       define HUGO_PIN_SS
//#       define HUGO_PIN_VREF

//#       define HUGO_PIN_LED_B

#       if defined(__AVR_ATtiny412__)
#           define IS_I2C_ALTERNATIVE false
#        else
#           define HUGO_PIN_LED_A PIN_PA4
#           define HUGO_PIN_LED_RED HUGO_PIN_LED_A
#           define HUGO_PIN_SHIELD_POWER PIN_PB1

#            define IS_I2C_ALTERNATIVE true
#       endif
#       define IS_UART_ALTERNATIVE false
#   else
#       define HUGO_PIN_D1 PIN_PA1
#       define HUGO_PIN_D2 PIN_PA2
#       define HUGO_PIN_D3 PIN_PA3
#       define HUGO_PIN_D4 PIN_PA4
#       if HUGO_PCB_VERSION == 7
#           define HUGO_PIN_D5 PIN_PA5
#       elif HUGO_PCB_VERSION == 8
#           define HUGO_PIN_D5 PIN_PB2
#       else
#           define HUGO_PIN_D5 PIN_PA6
#           define HUGO_PIN_D6 PIN_PB2
#       endif
#       define HUGO_PIN_RXD PIN_PA2 //alternative RXD
#       define HUGO_PIN_TXD PIN_PA1 //alternative TXD

#       define HUGO_PIN_SDA PIN_PB1
#       define HUGO_PIN_SCL PIN_PB0

#       define HUGO_PIN_MOSI  PIN_PA1
#       define HUGO_PIN_MISO PIN_PA12
#       define HUGO_PIN_SCK PIN_PA3
#       define HUGO_PIN_SS PIN_PA4
#       if HUGO_PCB_VERSION == 7
#           define HUGO_PIN_LED_A PIN_PA6
#           define HUGO_PIN_VREF PIN_PA5
#           define HUGO_PIN_LED_B PIN_PB3
#           define HUGO_PIN_SHIELD_POWER PIN_PB2
#       elif HUGO_PCB_VERSION == 8
#           define HUGO_PIN_LED_A PIN_PA6
#           define HUGO_PIN_LED_B PIN_PA7
#           define HUGO_PIN_SHIELD_POWER PIN_PB3
#       else
#           define HUGO_PIN_LED_A PIN_PA5
#           define HUGO_PIN_LED_B PIN_PA7
#           define HUGO_PIN_SHIELD_POWER PIN_PB3
#       endif
#       define HUGO_PIN_LED_RED HUGO_PIN_LED_A
#       define HUGO_PIN_LED_GREEN HUGO_PIN_LED_B
#
#       define IS_I2C_ALTERNATIVE false
#       define IS_UART_ALTERNATIVE true
#   endif
#endif

inline void hugo_gpio_init_serial(){
#if !defined(__AVR_ATtiny412__) && HUGO_PCB_VERSION < 7
  pinMode(HUGO_PIN_D2, INPUT); //to be used PB3 and PB2 instead
  pinMode(HUGO_PIN_D1, INPUT);
#else
  pinMode(HUGO_PIN_D2, INPUT_PULLUP);
  pinMode(HUGO_PIN_D1, OUTPUT);
#endif

    if (IS_UART_ALTERNATIVE){
#if !defined(__AVR_ATtiny424__) && !defined(__AVR_ATtiny824__) && !defined(__AVR_ATtiny1624__) && !defined(__AVR_ATtiny3224__)
        PORTMUX.CTRLB |= PORTMUX_USART0_ALTERNATE_gc; //_ATtiny414 uses alternative ports for i2c because of conflict with the POWER_SAVE_PIN
#else
        //NOTE: ports swapped in BleShield::init
        //PORTMUX.USARTROUTEA |= PORTMUX_USART1_NONE_gc;
        //PORTMUX.USARTROUTEA |= PORTMUX_USART0_ALT1_gc; //all 24s use alternative UART as sane as 14s. 24s use different name for the same value as 14s
#endif
    }
}

inline void hugo_gpio_initialize(){
    //set all pins as pulled-up inputs to reduce power consumption
    pinMode(PIN_PA1, INPUT_PULLUP);
    pinMode(PIN_PA2, INPUT_PULLUP);
    //pinMode(PIN_PA3, INPUT_PULLUP);
#if !defined(__AVR_ATtiny412__)
    pinMode(PIN_PA4, INPUT_PULLUP);
    pinMode(PIN_PA5, INPUT_PULLUP);
    pinMode(PIN_PB0, INPUT_PULLUP);
    pinMode(PIN_PB1, INPUT_PULLUP);
    pinMode(PIN_PB2, INPUT_PULLUP);
    pinMode(PIN_PB3, INPUT_PULLUP);

    pinMode(HUGO_PIN_LED_A, OUTPUT);
    digitalWrite(HUGO_PIN_LED_A, false);
#   if HUGO_PCB_VERSION >= 7
        pinMode(HUGO_PIN_SHIELD_POWER, OUTPUT);
        digitalWrite(HUGO_PIN_SHIELD_POWER, 1);
        pinMode(HUGO_PIN_LED_B, OUTPUT);
        digitalWrite(HUGO_PIN_LED_B, false);
#else
    pinMode(PIN_PA7, INPUT_PULLUP);
#   endif

    if (IS_I2C_ALTERNATIVE){
#   if !defined(__AVR_ATtiny424__) && !defined(__AVR_ATtiny824__) && !defined(__AVR_ATtiny1624__) && !defined(__AVR_ATtiny3224__)
        PORTMUX.CTRLB |= PORTMUX_TWI0_ALTERNATE_gc; //_ATtiny414 uses alternative ports for i2c because of conflict with the POWER_SAVE_PIN
#   endif
    }

    hugo_gpio_init_serial(); //just for sure. it was here for previous versions <7
#else
    pinMode(PIN_PA6, INPUT_PULLUP);
    pinMode(PIN_PA7, INPUT_PULLUP);
#endif
}

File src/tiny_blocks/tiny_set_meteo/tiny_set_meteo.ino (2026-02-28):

/*
BOARD: hugo_adapter-i2c-pull-ups driving ble-shield, power-block and ambient-block (+ display block optionally)
Chip: ATtiny1614
Clock Speed: 1 - 10MHz
Programmer: jtag2updi (megaTinyCore)
*/

//#define WIND_AND_RAIN
//#define USE_DISPLAY
//#define GET_CHARGING
//#define GET_PRESSURE

#include <avr/sleep.h>

#include <stdint.h>
#include <Arduino.h>
#include <hugo_defines.h>
#include <hugo_utils.h>
#include <tiny_main_base.h>
#include <tiny_main_ambient.h>
#include <tiny_ble_shield.h>
#include <tiny_main_power.h>
#include <tiny_main_rj12.h>

#ifdef USE_DISPLAY
# include <tiny_main_display.h>
#endif

#define MESH_MAIN_NODE_ID 0x04
#define RJ12_RAIN_GAUGE_ID 0x30
#define RJ12_WIND_BLOCK_ID I2C_BLOCK_TYPE_ID_RJ12

// 0,   22,5  45,   67.5, 90, 112.5,  135,  157.5,  180,  202.5 225,  247.5,  270,  292.5,  315,  337.5
// 22k, 33k, 6k8,  8k2,  820,  1k, 680,,   2k2,  1k5,    3k9,  3k3,  15k,  12k,    120k  42k,    68k
static uint16_t wind_vane_values[16] = {143, 301, 259, 637, 607, 946, 831, 888, 707, 789, 417, 471, 100, 111, 84, 198};

uint8_t multiplier = 5;

tiny_common_buffer_t* buffer = tiny_main_base_get_common_buffer();

#define DEC_NR_BUFFER_SIZE 8
static char s_dec_nr_buffer[DEC_NR_BUFFER_SIZE];

static bool heartbeat = false;
BleShield ble_shield;

//#define WIND_AND_RAIN
#ifdef WIND_AND_RAIN
bool s_rain_block_available = false;
bool s_wind_block_available = false;

static uint32_t km_h = 0;
static uint16_t wind_vane_value = 0;
static uint16_t rain_amount = 0;
#endif

static int32_t s_temperature = 0;
static int32_t s_pressure = 0;
static int32_t s_humidity = 0;

static charging_state_t s_charging_state = {0, 0};
static int32_t s_voltage_mV = 0;
static int32_t s_current_uA = 0;

pocketBME280& bme = tiny_main_ambient_bme();

char* fill_decimal_number(int32_t number, uint16_t decimal_shift, uint8_t precision = 4){
  s_dec_nr_buffer[DEC_NR_BUFFER_SIZE-1] = '\0';
  char buffer_pos = DEC_NR_BUFFER_SIZE - 1;
  bool negative = number < 0;
  if (negative){
    number = -number; //number is abs now
  }
  bool dot_present = false;
  while (true){
    if (number == 0){
      s_dec_nr_buffer[--buffer_pos] = '0';
      if (decimal_shift == 0){
        break;
      }
    }

    uint8_t digits = 0;
    uint32_t temp = number;
    while (true){
      if (temp == 0){
        break;
      }
      if (decimal_shift == 0){ //remains integer only
        s_dec_nr_buffer[--buffer_pos] = '0' + temp % 10;
      }
      else{
        digits++;
      }
      temp /= 10;
    }

    if (decimal_shift == 0){ //whole number was already processed
      break;
    }

    uint8_t lost_nr = number % 10;
    number /= 10;

    if (digits > precision){
      if (lost_nr > 4){
        number += 1; //rounding
      }
    }
    else if (digits > 0){
       s_dec_nr_buffer[--buffer_pos] = '0' + lost_nr;
       precision--;
    }

    if (--decimal_shift == 0){
      s_dec_nr_buffer[--buffer_pos] = '.';
      dot_present = true;
    }
  }

  if (negative){
    s_dec_nr_buffer[--buffer_pos] = '-';
  }

  //remove redundant decimal zeros
  if (dot_present){
    uint8_t last_pos = DEC_NR_BUFFER_SIZE - 2;
    while (true){
      if (s_dec_nr_buffer[last_pos] == '0'){
        s_dec_nr_buffer[last_pos] = '\0';
      }
      else if (s_dec_nr_buffer[last_pos] == '.'){
        s_dec_nr_buffer[last_pos] = '\0';
        break;
      }
      else{
        break;
      }
      last_pos--;
    }
  }
  return s_dec_nr_buffer + buffer_pos;
}

void add_to_common_buffer(char const* text){
  uint8_t append_size = min((COMMON_BUFFER_SIZE - 1), strlen(text));
  strncpy((char*)(buffer->data + buffer->size), text, append_size);
  buffer->size += append_size;
  buffer->data[buffer->size] = '\0';
}

void publish_buffer(bool to_display){
#ifdef USE_DISPLAY
  if (to_display){
    display.println((char*)buffer->data);
  }
#endif

  ble_shield.send_mesh_data(MESH_MAIN_NODE_ID);
}

void publish_value(char const * variable, char const* value, char const* unit, bool to_display=true){
  buffer->size = 0;
  buffer->data[0] = '\0';
  add_to_common_buffer(variable);
  add_to_common_buffer("=");
  add_to_common_buffer(value);
  if (strlen(unit) > 0){
    add_to_common_buffer(" ");
    add_to_common_buffer(unit);
  }
  publish_buffer(to_display);
  //delay(100);
}

void setup()
{
  tiny_main_base_init();
  delay(200);//it is necessary to wait a while to all blocks and its extensions are started
  tiny_main_power_init(false);
  tiny_main_ambient_init_block();

#ifdef WIND_AND_RAIN
  s_rain_block_available = tiny_main_base_is_available(RJ12_RAIN_GAUGE_ID);
  s_wind_block_available = tiny_main_base_is_available(RJ12_WIND_BLOCK_ID);
#endif

#ifdef USE_DISPLAY
  tiny_main_display_init();
  display.clearDisplay();
  display.setTextSize(1);
  display.setTextColor(WHITE);
#endif

  ble_shield.init();

#ifdef WIND_AND_RAIN
  tiny_main_rj12_set_pin_mode(RJ12_WIND_BLOCK_ID, Rj12PinId::pin5, Rj12PinMode::input);
  tiny_main_rj12_set_pin_mode(RJ12_WIND_BLOCK_ID, Rj12PinId::pin4, Rj12PinMode::interrupt_rising);

  tiny_main_rj12_set_pin_mode(RJ12_RAIN_GAUGE_ID, Rj12PinId::pin4, Rj12PinMode::interrupt_rising);
  tiny_main_rj12_pin5_set_oscil_period_ms(RJ12_RAIN_GAUGE_ID, 100);
#endif

  delay(100); //give extra time to self-initialize all sensors
}

uint8_t get_closest_wind_direction_index(uint16_t measured){
  uint16_t closest_distance = abs(measured - wind_vane_values[0]);
  uint8_t closest_index = 0;
  for (uint8_t index = 1; index < 16; index++){
    uint16_t distance = abs(measured - wind_vane_values[index]);
    if (distance < closest_distance){
      closest_distance = distance;
      closest_index = index;
    }
  }
  return closest_index;
}
void process_power(){
  if (!tiny_main_power_is_available()){
    return;
  }

  tiny_main_power_power_on(true);
  delay(1);

#ifdef  GET_CHARGING
  s_charging_state = tiny_main_power_get_charging_state();
#endif

  uint8_t counter = 3;
  while (counter > 0) {
    s_voltage_mV = tiny_main_power_get_bat_voltage_mV();
    s_current_uA = tiny_main_power_get_bat_current_uA();
    if (s_voltage_mV > 1000){
      break;
    }
    counter--;
    delay(100);
  }

  tiny_main_power_power_on(false);

  // if (voltage_mV < 3400){
  //   multiplier = 10;
  // }
  // else if (voltage_mV < 3500){
  //   multiplier = 6;
  // }
  // else if (voltage_mV < 3700) {
  //   multiplier = 4;
  // }
  // else {
  //   multiplier = 3;
  // }
}
void warn(uint8_t count){
  delay(100); //to separate from another warning
  for(uint8_t index=0; index<count; index++){
    tiny_main_base_shine_red(true);
    delay(100);
    tiny_main_base_shine_red(false);
    delay(20);
  }
}
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

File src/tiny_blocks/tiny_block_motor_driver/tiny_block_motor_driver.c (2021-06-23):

/*
 * Copyright (c) 2021 jakub-vesely
 * This software is published under MIT license. Full text of the licence is available at https://opensource.org/licenses/MIT
 */

#include "tiny_block_motor_driver_arduino/motor_commands.h"
#include "tiny_block_motor_driver.h"
#include <lua.h>
#include <lualib.h>
#include <hugo_defines.h>
#include <i2c.h>
#include <hugo_tiny_block_defines.h>

static const char *TAG = "motor";

static void _send_command(lua_State* L, uint8_t command){
    LUA_PARAM_NR_CHECK(2);

    uint8_t address = lua_tointeger(L, 1);
    uint8_t motor_id = lua_tointeger(L, 2);

    ESP_LOGI(TAG, "sent command %d to address: %d with data %d", command, address, motor_id);

    hugo_i2c_tiny(address, I2C_BLOCK_TYPE_ID_MOTOR_DRVR, command, &motor_id, 1, NULL, 0);
}

static int32_t _get_counter(lua_State* L){
    LUA_PARAM_NR_CHECK(2);

    uint8_t address = lua_tointeger(L, 1);
    uint8_t in_data[4];
    uint8_t motor_id = lua_tointeger(L, 2);
    if (!hugo_i2c_tiny(address, I2C_BLOCK_TYPE_ID_MOTOR_DRVR, I2C_MOTOR_GET_COUNTER, &motor_id, 1, in_data, 4)){
        ESP_LOGE(TAG, "no counter provided - for %d", address);
        return 0; //data are invalid it is better t to return a particular value than a random one
    }

    ESP_LOGI(TAG, "received_data %d %d %d %d", in_data[0], in_data[1], in_data[2], in_data[3]);

    int32_t counter = 0;
    for (uint8_t index = 0; index < 4; ++index){
        counter |= in_data[index] << index * 8;
    }

    return counter;
}

static int cl_motor_turn_clockwise(lua_State* L){
   _send_command(L, I2C_MOTOR_TURN_CLOCKWISE);
    return 0;
}

static int cl_motor_turn_anticlockwise(lua_State* L){
   _send_command(L, I2C_MOTOR_TURN_ANTICLOCKWISE);
    return 0;
}

static int cl_motor_stop(lua_State* L){
   _send_command(L, I2C_MOTOR_STOP);
    return 0;
}

static int cl_motor_power_off(lua_State* L){
   _send_command(L, I2C_MOTOR_POWER_OFF);
    return 0;
}

static int cl_motor_power_on(lua_State* L){
   _send_command(L, I2C_MOTOR_POWER_ON);
    return 0;
}

static int cl_motor_reset_counter(lua_State* L){
   _send_command(L, I2C_MOTOR_RESET_COUNTER);
    return 0;
}

static int cl_motor_get_counter(lua_State* L){
   lua_pushinteger(L, _get_counter(L));
   return 1;
}

static int cl_motor_speed_100(lua_State* L){
   _send_command(L, I2C_MOTOR_SET_SPEED_100);
    return 0;
}

static int cl_motor_speed_80(lua_State* L){
   _send_command(L, I2C_MOTOR_SET_SPEED_80);
    return 0;
}

static int cl_motor_speed_60(lua_State* L){
   _send_command(L, I2C_MOTOR_SET_SPEED_60);
    return 0;
}

static int cl_motor_speed_40(lua_State* L){
   _send_command(L, I2C_MOTOR_SET_SPEED_40);
    return 0;
}

static int cl_motor_speed_20(lua_State* L){
  _send_command(L, I2C_MOTOR_SET_SPEED_20);
    return 0;
}

static int cl_motor_speed_0(lua_State* L){
   _send_command(L, I2C_MOTOR_SET_SPEED_0);
    return 0;
}

bool tiny_motor_block_init(lua_State* L){
    REGISTER_LUA_FUNCTION(L, cl_motor_turn_clockwise);
    REGISTER_LUA_FUNCTION(L, cl_motor_turn_anticlockwise);
    REGISTER_LUA_FUNCTION(L, cl_motor_stop);
    REGISTER_LUA_FUNCTION(L, cl_motor_power_off);
    REGISTER_LUA_FUNCTION(L, cl_motor_power_on);
    REGISTER_LUA_FUNCTION(L, cl_motor_reset_counter);
    REGISTER_LUA_FUNCTION(L, cl_motor_get_counter);
    REGISTER_LUA_FUNCTION(L, cl_motor_speed_100);
    REGISTER_LUA_FUNCTION(L, cl_motor_speed_80);
    REGISTER_LUA_FUNCTION(L, cl_motor_speed_60);
    REGISTER_LUA_FUNCTION(L, cl_motor_speed_40);
    REGISTER_LUA_FUNCTION(L, cl_motor_speed_20);
    REGISTER_LUA_FUNCTION(L, cl_motor_speed_0);
    return true;
}

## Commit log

2020-05-24 simple example (proof of concept) of calling LUA code from esp-idf C code. It seems it will work and intended SW design is possible.
    [partitions.csv]
2020-05-24 added first module build_in_led with one method main stack has be increased because 7 was too low to call "require" package
    [partitions.csv]
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2020-06-04 added functionality for chassis + fixed typo
    [built_in_led.c, chassis.c, gpio.c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]
2020-06-24 refactoring - modules moved to components directory to by aligned with Lua rules added event_loop component
    [partitions.csv]
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2020-07-27 i2c_wrapper renamed to i2c because there is no conflict with ESP's i2c driver + minor fixes
    [main.c]
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2020-11-28 I2C messages are processed over event loop - prevent conflicts
    [hugo.skp]
2020-11-28 esp repated sources moved to the esp subdirectory was added directory for tiny_blocks
    [partitions.csv]
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2020-12-23 updated eagle pcbs + added docs
    [3x3.brd, block_base_L.brd, block_base_L.sch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]
2020-12-31 completed pcb design for M.0 - made PCB order
    [4x4_M.brd, block_base_M.brd, block_base_M.sch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]
2021-01-15 changes in pcb desingm - not finished and another minor changes in the documentation
    [block_base_M.brd, block_base_M.sch, block_base_S.brd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]
2021-01-16 PCB subfolder restructured to the type_id_letter_name format
    [L_A_jumper_bed.brd, L_A_jumper_bed.sch, L_B_block_base.brd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]
2021-02-04 pcb M.1 -not finished
    [M_3x4.brd, M_A_jumper_bed.brd, M_A_jumper_bed.sch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]
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2021-02-28 updateed PCBs - adjustments based on usage of version 1
    [M_A_jumper_bed.brd, M_A_jumper_bed.sch, M_B_block_base-rotated.brd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]
2021-02-28 repository reorganisation .ino are sored in appropriate esp components
    [3x3.brd, L_A_jumper_bed.brd, L_A_jumper_bed.sch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]
2021-02-28 motor - path name adjustments
    [M_G_ext_motor.brd, M_G_ext_motor.sch]
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2021-04-02 adjusted 90° connector postition to be possible to cut to 1x3 easyly
    [M_A_base.brd]
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2021-05-10 updated PCBS after the version 1 delivery
    [M_A_base.brd, M_C_ext_main.brd, M_C_ext_main.sch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]
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2021-05-22 repository structure reorganized (tiny-blocks moved to a separate directory) implemented tiny-power-block
    [M_D_ext_power.brd, M_D_ext_power.sch]
2021-05-22 updated PCBs after delivery of v1
    [M_A_base.brd, M_A_base.sch, M_C_ext_main_cp2102.brd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]
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2021-06-23 updated PCBs for version 2
    [M_A_base.brd, M_C_ext_main.brd, M_C_ext_main.sch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]
2021-07-23 ble support + downloading lua files
    [partitions.csv]
2021-08-21 closed PCB version M.2
    [M_3x4._v2brd.brd, M_B_adapter.brd, M_C_ext_main.brd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]
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2021-10-02 tiny blodk sources moved out of the deprecated src
    [partitions.csv]
2021-10-27 updated power module to be handled charging correctly (LED + attiny pin)
    [M_D_ext_power.brd, M_D_ext_power.sch]
2021-10-27 fixed long delay in calling planned tasks. fixed handling ESC removed unnecessary prints
2021-11-12 added python code for power block refactoring i2c calls - run until complete doesn't work from async environment. improved active variable lot of small improvements adjusted another toold to be adjus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
    [M_D_ext_power.brd, M_D_ext_power.sch]
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2021-12-27 button block + chassis + default i2c addresses
    [M_A_base.brd, M_D_ext_power.brd, M_D_ext_power.sch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]
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2021-12-28 inverted logic of power switch to be left for off and right for on
    [M_D_ext_power.brd, M_D_ext_power.sch]
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2022-01-22 added Smoother class, it should limit a sensor noise. RAM consumtion optimization
2022-01-29 eliminate error messages when block is not connected - user should be just infromed that block is not avaialbe added distance block added power save to tiny-blocks smoother changed to smoothed_variab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
    [tiny_block_button.ino, tiny_block_distance.ino, tiny_block_ir.ino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]
2022-01-29 updated main board - added 5 to 3.3V regulator becaues one in CP is too weak updated power board - added shotky diode to FET to be sure it works as expected
    [M_C_ext_main.brd, M_C_ext_main.sch, M_C_ext_main_cp2102.sch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]
2022-03-30 PCB's adjustments + sensor extension
    [M_E_ext_proto.brd, M_E_ext_proto.sch, M_E_ext_sensor.brd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]
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2022-04-03 bugfix: when user built two different project files from another could remains in .build folder removed unused import (inserted probably automatically by IDE)
2022-04-15 moved sd-card closer to border - it was difficult to insert it.
    [M_I_ext_sound.brd]
2022-04-15 bugfixes: log level + uploading is terminated in case of a build issue
2022-04-22 finishing PCB release M.v3 - not done yet
    [M_3x4._v3.brd, M_I_ext_sound_power_save.brd, M_I_ext_sound_power_save.sch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]
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2022-06-01 main and switch pcbs adjusted
    [M_C_ext_main.brd, M_C_ext_main.sch, M_L_ext_5w_switch.brd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]
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2022-07-04 power ext board adjustments - mainly replacement of charging info MOSFET - PMOS to NMOS switch position adjustment
    [M_D_ext_power.brd, M_D_ext_power.sch]
2022-07-04 adapter board with AtTiny-414
    [M_B_adapter_414.brd, M_B_adapter_414.sch]
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2022-07-04 bugfix: USB flag while charging
    [tiny_block_power.ino]
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2022-09-16 updated for PCB version 4
    [M_B_adapter_414.brd, M_B_adapter_414.sch, M_D_ext_power.brd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]
2022-09-26 bugfixes: * in case of restart from ble, program starts after ble is connected again to be all logs provided to HugoTerminal * verbose logs just in case they are required * logs
    features:
    * files used in the project are imported only
2022-09-26 collection of PCBs for v4 started
    [M_3x4._v4.brd, M_B_adapter_414.brd, M_B_adapter_414.sch]
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2022-10-29 version without most of milling
    [M_3x4._v4.2.brd]
2023-01-02 not finished meteo block
    [M_N_ext_connector.sch]
2023-01-02 minor fixes
    [M_B_adapter_414.brd, M_B_adapter_414.sch, M_N_ext_connector.brd]
2023-01-14 beating to meteo + fix on dashoblard connector
2023-02-16 changed one data bit to be compatible with T-micro32+
    [M_C_ext_main.brd, M_C_ext_main.sch]
2023-02-16 3.3V fuse moved before stabilizer to be final voltage as expected 3.3V. the fuse can loose up to 0.3V
    [M_D_ext_power-solar1.brd, M_D_ext_power-solar1.sch]
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2023-07-23 pull-up resistors for i2c
    [M_B_adapter.brd, M_B_adapter.sch]
2023-07-23 bugfix: switched serial TX-RX
    [M_B_adapter_414.brd, M_B_adapter_414.sch]
2023-07-23 changes in values LM3671_3.3 -> MCP1603T-330I
    [M_C_ext_main.brd, M_C_ext_main.sch]
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2023-07-23 removed files commited by mistake
    [M_D_ext_power-solar1.brd, M_D_ext_power-solar1.sch]
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2023-07-31 bugfix: handle case where expected length is 0 and the length is part of the message added ble_block
    [tiny_block_ble.ino]
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2023-12-06 changed type of 3.3V converter back to LM3671
    [M_D_ext_power-solar.brd, M_D_ext_power-solar.sch]
2023-12-25 bugfix: swapped GPIOs to be handled interrups during slepp
    [M_M_ext_meteo_RJ11.brd, M_M_ext_meteo_RJ11.sch]
2024-01-15 bugfix: is_charging displayed opposite values
    [tiny_main_power.cpp]
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2024-02-29 bugfix: corrected is_charging flag
    [tiny_main_power.cpp]
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2024-02-29 rj12 bugfixes: pin interrupts should be recorded correctly now * including erasing counter and * timestamps during sleep
    [tiny_block_rj12.ino, tiny_main_rj12.cpp, tiny_set_meteo.ino]
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2024-05-12 bugfix: positive values had wrong value
    [tiny_main_power.cpp]
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2024-06-04 fet gates resistor increased to 390 k - lower power consumption
    [M_D_ext_power-solar.brd, M_D_ext_power-solar.sch]
2024-06-04 main with ftdi instead of cp - it is cheaper
    [M_C_ext_main_ftdi.brd, M_C_ext_main_ftdi.sch]
2024-07-16 usb moved to be possible to place in connected adapters
    [M_D_ext_power-solar.brd]
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2024-09-14 PCB v7 * 14 pin attiny is main adapter chip now. * changed adapter pin meaning (a1-a5, swapped RX-TX, VUSB replaced by A5, top most pin changed from GND to A4) * changed usb chip of main board
    [M_3x4._v7.brd, M_B_adapter.brd, M_B_adapter.sch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]
2024-10-01 MCP1603T-330I changed to LM3671_3.3
    4u7 moved close to input of LM3671_3.3
    [M_C_ext_main.brd, M_C_ext_main.sch, M_C_ext_main_cp2102N.brd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]
2024-10-18 * LED2 is connected to PA7 (was PB3) * GPIO pins renamed to D1 - D5 * fixed MISO typo (should be MOSI for PA1)
    [M_B_adapter.brd, M_B_adapter.sch]
2024-10-18 gpio.h + fixed dir name for fiveWaySwitch modified megaTinyCore with HUGO_PCB_VERSION is expected
    [hugo_gpio.h, tiny_block_ble.ino, tiny_block_button.ino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]
2024-10-18 updated resistor values for leds + led test
    [M_B_adapter.brd, M_B_adapter.sch]
2024-11-29 adjusted tiny_set_meteo to be more reliable minor fixes for older pcb versions
    [hugo_gpio.h, tiny_block_power.ino, tiny_main_base.cpp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]
2025-01-26 added possibility to connect accumulator via adapter pin
    [M_D_ext_power.brd, M_D_ext_power.sch]
2025-01-26 changed power sleep transistor to p-channel added tssop version for attiny v2 chips
    [M_B_adapter-tssop.brd, M_B_adapter-tssop.sch]
2025-01-26 added shottky diode to vcc connection of another power block without connected power via USB leads to oscillations
    [M_C_ext_main.brd, M_C_ext_main.sch, M_C_ext_main_cp2102N.brd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]
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2025-03-16 HugoTinyWireInitialize moved before setting pin to doesn't be rewritten
    [tiny_block_distance.ino]
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2025-03-16 fixed source file name to be aligned with the folder name
    [tiny_block_five_way_switch.ino, tiny_five_way_switch.ino]
2025-05-03 redesigned motor driver
2025-07-21 version 8 main changes * ideal diode separated 3v3 DC-DC to protect it from back current * smaller package of ina 219 * usage of tssop attiny v2 in adapter * and change of PA5 to PB2 with ^ and ~ (or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
    [M_3x4._v8.brd, M_B_adapter-tssop.brd, M_B_adapter-tssop.sch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]
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2026-02-10 fixed RX-TX
    [M_O_ext_bluetooth_JDY25.brd, M_O_ext_bluetooth_JDY25.sch]
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2026-02-13 fixed power save for jdy
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2026-03-08 PA4 holds power up. PB2 monitors pressing the power button. The idea is that when user press the power button attiny will hold the power. when user press it second time attiny stops the holding.
    [M_D_ext_power.brd, M_D_ext_power.sch]
2026-03-16 turning on/off is performed by monitoring push button. D flip-flop is not necessary - has problem with button oscilations.
    [M_D_ext_power-with_d.brd, M_D_ext_power-with_d.sch, M_D_ext_power_usb_centered_M9.brd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]
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

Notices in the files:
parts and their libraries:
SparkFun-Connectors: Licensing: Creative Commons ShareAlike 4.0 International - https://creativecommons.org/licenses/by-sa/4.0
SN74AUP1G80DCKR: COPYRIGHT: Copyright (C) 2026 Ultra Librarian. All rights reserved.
